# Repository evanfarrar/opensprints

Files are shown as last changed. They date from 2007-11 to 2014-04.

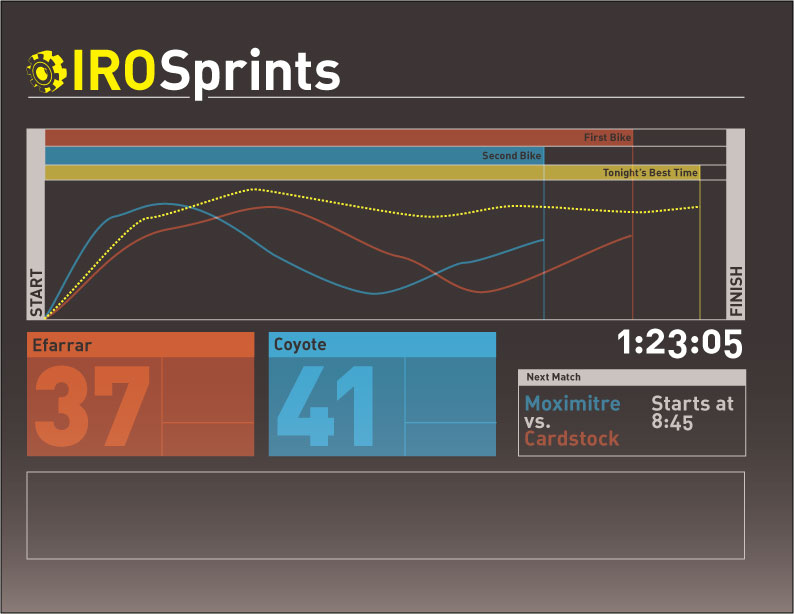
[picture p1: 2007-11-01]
doc/interface_mockups/mockup.png

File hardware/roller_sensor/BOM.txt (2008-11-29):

Qty	Descr					Mfr			Mfr P/N			Vendor		Vendor P/N	
---	-------------------		-------		-----------		-------		------------
1	hall effect switch		Allegro		A3245LUA-T		digikey		620-1213-ND
1	RJ45 modular jack		tyco		5555164-1		digikey		5555164-1
														mouser		571-5555164-1
1	5mm Red or Blue LED									digikey		365-1180-ND
1	330 ohm resistor
	(for Red LED)
	or
	100 ohm resistor									digikey		100EBK-ND
	(for Blue LED)
1	1 uF bypass cap										digikey		478-3192-ND or 490-3810-ND
2

http://search.digikey.com/scripts/DkSearch/dksus.dll?Detail?name=620-1213-ND
http://search.digikey.com/scripts/DkSearch/dksus.dll?Detail?name=A31442-ND
http://search.digikey.com/scripts/DkSearch/dksus.dll?Detail?name=365-1180-ND
http://search.digikey.com/scripts/DkSearch/dksus.dll?Detail?name=100EBK-ND
http://search.digikey.com/scripts/DkSearch/dksus.dll?Detail?name=478-3192-ND

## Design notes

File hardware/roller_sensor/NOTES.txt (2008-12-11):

NOTES:
 * board dimensions: 1.4" x 2"

TODO: for v2:
 * schematic:
   - 
 * board:
   - silk screen labels 
 * source repository: 
   - get rid of .cam file not being used.
   - create Makefile
     -- make schem-print
     -- make schem-pdf
     -- make board-print
     -- make board-pdf
     -- make gerb (moves created files to gerber/ dir) 
     -- make archive

DONE:
 * now has 2 LEDs
   - one 5 mm LED for signaling when the HE sensor is triggered.
   - one 3 mm LED for power indicator.
   - make grid of through-hole pads. qty = 7 * 14 - 12
 * board:
   - resistors should lie down instead of standing up, per the request of Jonathan Morrison.
   - new board dimensions 1.4" x 2.0"
   - make grid of through-hole pads. qty = 7 * 14 - 12
 * only 1 screw hole

misc notes:
 * Ethernet cable wiring:
   - http://en.wikipedia.org/wiki/10BASE-T
   - http://en.wikipedia.org/wiki/8P8C#Applications

Barebonespcb.com
#  2-layer, FR-4, 0.062" thick
# All-holes-plated
# 6-mil line/gap minimum
# Tin finish over 1-oz Copper
# No internal routing or scoring
(including mouse bites)
# Cut to rectangle shape only
# No mask
# No legend
# Min size 1.25" X 1.25"
# Max size 12" X 16" or 192 sq. in.
# Gerber 274X preferred
# Excellon drill (English Units)
# Minimum hole size 0.015

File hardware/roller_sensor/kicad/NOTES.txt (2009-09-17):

printing:
To print a drawing of the layout, print to pdf with X and Y scaling 1.0. Then print the generated PDF at 1.077 scale.

The mounting hole is a single pad with diameter 0.26" with a pad diameter 0.26".

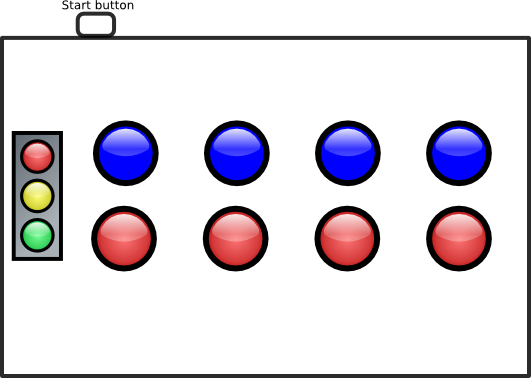
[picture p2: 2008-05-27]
doc/interface_mockups/physical_mock2.png

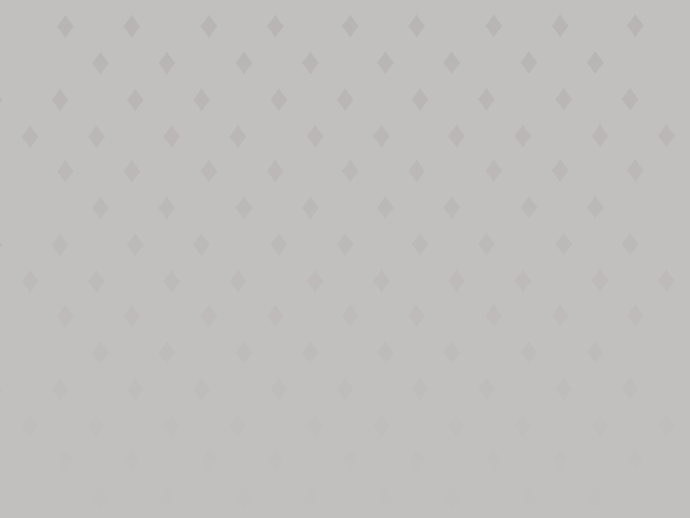
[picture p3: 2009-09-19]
media/skins/math_rash/background_menus.png

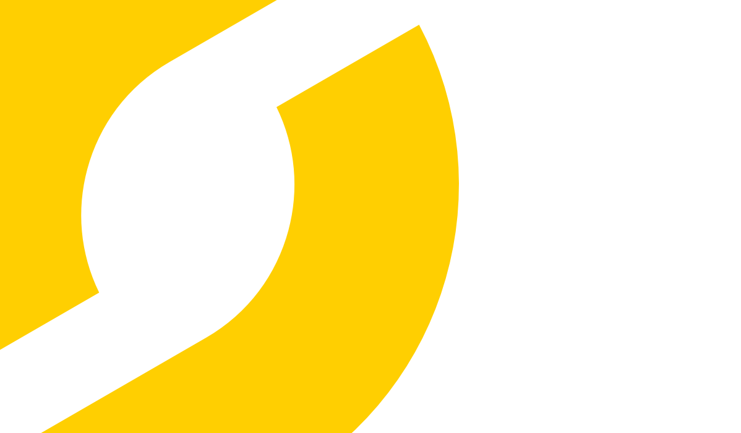
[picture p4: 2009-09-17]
media/background.png

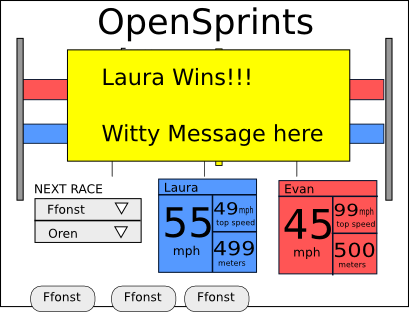
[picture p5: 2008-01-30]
doc/interface_mockups/2.0/after_race.png

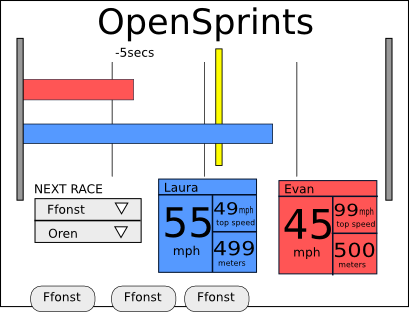
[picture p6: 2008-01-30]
doc/interface_mockups/2.0/in_progress.png

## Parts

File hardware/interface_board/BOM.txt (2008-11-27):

Qty   Descr                   Mfr         Mfr P/N         Supplier    Supplier P/N	
---   ------------------      -------     -------------   ---------   ------------
1     plastic box             Serpac      A31             Digi-Key    SRA31G-ND
4     RJ45 modular jack       tyco        5555164-1       Digi-Key    5555164-1
                                                          Mouser      571-5555164-1

2     male breakaway
      headers 8 pos

2     male breakaway
      headers 6 pos

x     hook-up wire

(Optional:)

2     screw terminal
      blocks

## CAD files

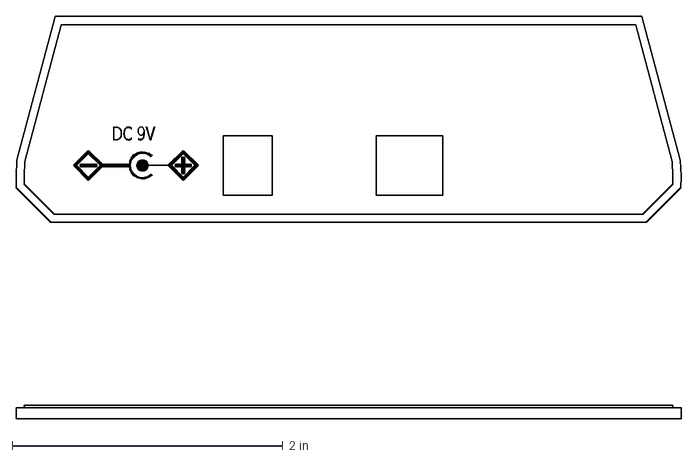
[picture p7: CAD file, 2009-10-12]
hardware/a-31_modifications/panel-arduino_text.dxf
DC\~9V

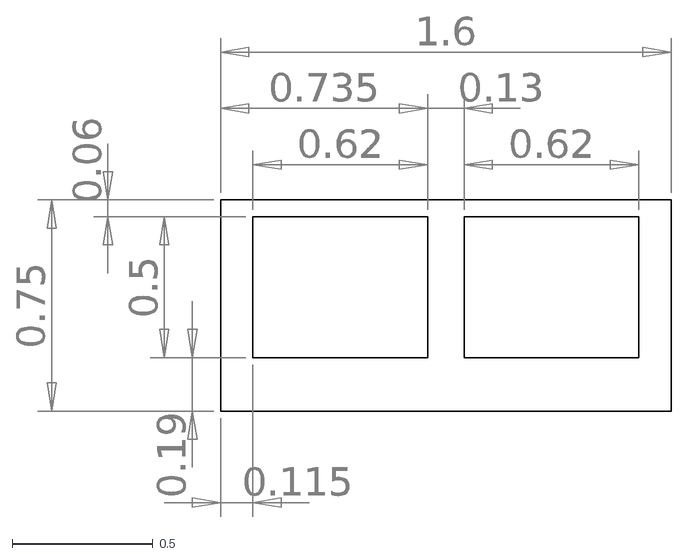
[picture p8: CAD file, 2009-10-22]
hardware/c-6_modifications/c-6_RJ45_cutouts.dxf
0.75
0.06
0.5
0.19
1.6
0.735
0.13
0.62
0.115

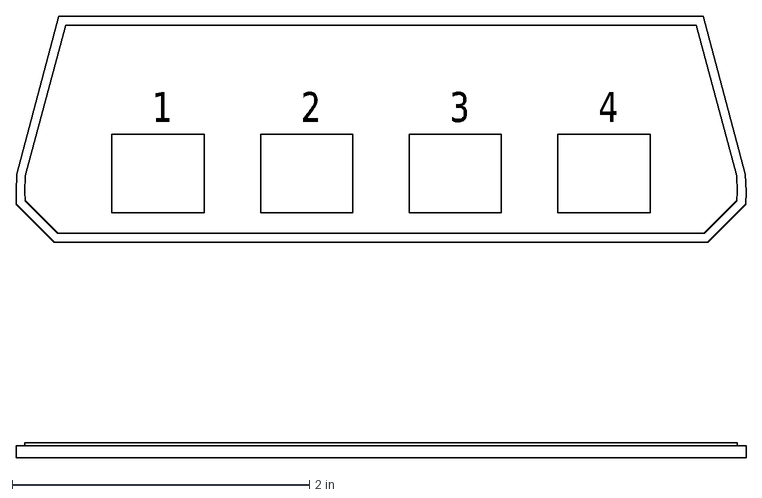
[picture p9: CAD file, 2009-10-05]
hardware/a-31_modifications/panel-sensors_text.dxf
1
2
3
4

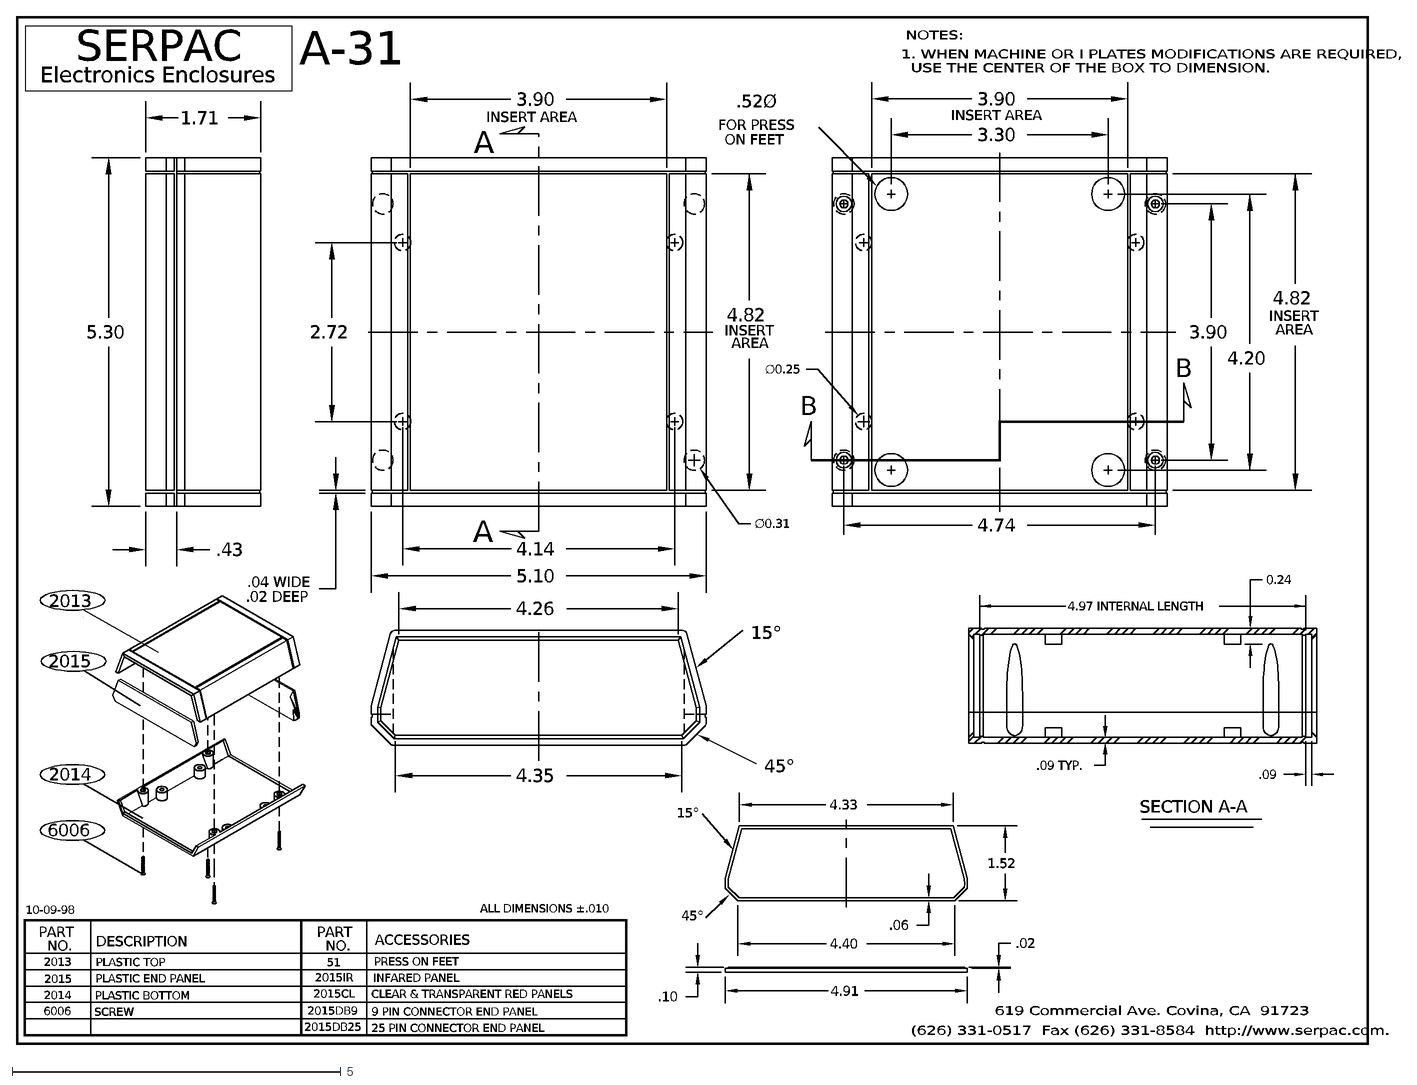
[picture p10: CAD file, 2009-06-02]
hardware/a-31_modifications/a-31.dxf
1.52
(626) 331-0517 Fax (626) 331-8584 http://www.serpac.com.
PLASTIC BOTTOM
PLASTIC TOP
DESCRIPTION
PLASTIC END PANEL
2014
6006
2013
2015
NO.
SCREW
10-09-98
PART
ALL DIMENSIONS ±.010
CLEAR & TRANSPARENT RED PANELS
2015CL
2015IR
51
ACCESSORIES
PRESS ON FEET
INFARED PANEL
4.35
45°
.10
15°
4.91
4.40
4.33
.06
619 Commercial Ave. Covina, CA 91723
SECTION A-A
.02
.09 TYP.
.09
3.90
3.30
INSERT AREA
USE THE CENTER OF THE BOX TO DIMENSION.
4.74
1. WHEN MACHINE OR I PLATES MODIFICATIONS ARE REQUIRED,
SERPAC
Electronics Enclosures
5.30
2.72
.43
.02 DEEP
.04 WIDE
4.26
A
5.10
4.14
A-31
1.71
INSERT
4.82
AREA
B
ON FEET
FOR PRESS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

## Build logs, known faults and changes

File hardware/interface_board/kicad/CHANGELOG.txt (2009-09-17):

---------------------------------------------------
v2.3.2 2009.09.13
---------------------------------------------------
gerbers generated with Pcbnew Build: SVN-R1805 (20090603)

Changes:

    * added blink LED to design
	* designed for soldermask and silkscreen for the first time.
	* font has curves

---------------------------------------------------
v2.2
---------------------------------------------------

Changes:

    * FIXED: The Arduino's power jack doesn't poke through the end panel of the enclosure.
          o Moves the Arduino out 0.05". 
    * improved indication of the columns of holes where the male headers are installed.
    * now text says "opensprints.org" instead of "OpenSprints". 

---------------------------------------------------
Previous version: v2.1
---------------------------------------------------

Changes:

    * Arduino placement moved so it fits better inside the enclosure.
    * Mounting holes for affixing the Arduino to the board with small nuts and bolts.
    * "top" and "bottom" labels.
    * Aesthetic changes to the title text. 

Bugs:

    * The Arduino's power jack doesn't poke through the end panel of the enclosure. 

---------------------------------------------------
Previous version: v2
---------------------------------------------------
Changes:

    * Phased out UBW support.
    * Designed to fit a specific plastic project box.
    * Moved the placement of the RJ45 jacks to provide better access to the tabs. 

Bugs:

    * The Arduino is positioned too far out. A slot must be routed out of the end panel to fit the panel in the enclosure. 

---------------------------------------------------
First version: v1
---------------------------------------------------

This version supported both the UBW and the Arduino microcontroller boards. NOTE: V1 interface board rework

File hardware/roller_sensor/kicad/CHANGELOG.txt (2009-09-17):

v2.2.3 2009.09.13
---------------------------------------------------
gerbers generated with Pcbnew Build: SVN-R1805 (20090603)

Changes:

    * VOUT and VCC signals going to hall effect sensors can now be swapped in order to allow the user to install hall effect sensor backwards, which swaps the magnetic pole that the sensor senses.
	* designed for soldermask and silkscreen for the first time.
	* font has curves

v2.1
---------------------------------------------------
Changes:

    * Sensor indicator LED wiring issue was corrected.
    * "top" and "bottom" labels. 

Bugs:

    * TBD 

v2
---------------------------------------------------
Changes:

    * Designed to fit a specific plastic project enclosure.
    * Added power indicator LED.
    * Moved the placement of the RJ45 jacks to provide better access to the tabs. 

Bugs:

    * Ouch! The sensor trigger indicator LED was wired incorrectly. 

First version: v1
---------------------------------------------------
Worked fine, wired correctly.

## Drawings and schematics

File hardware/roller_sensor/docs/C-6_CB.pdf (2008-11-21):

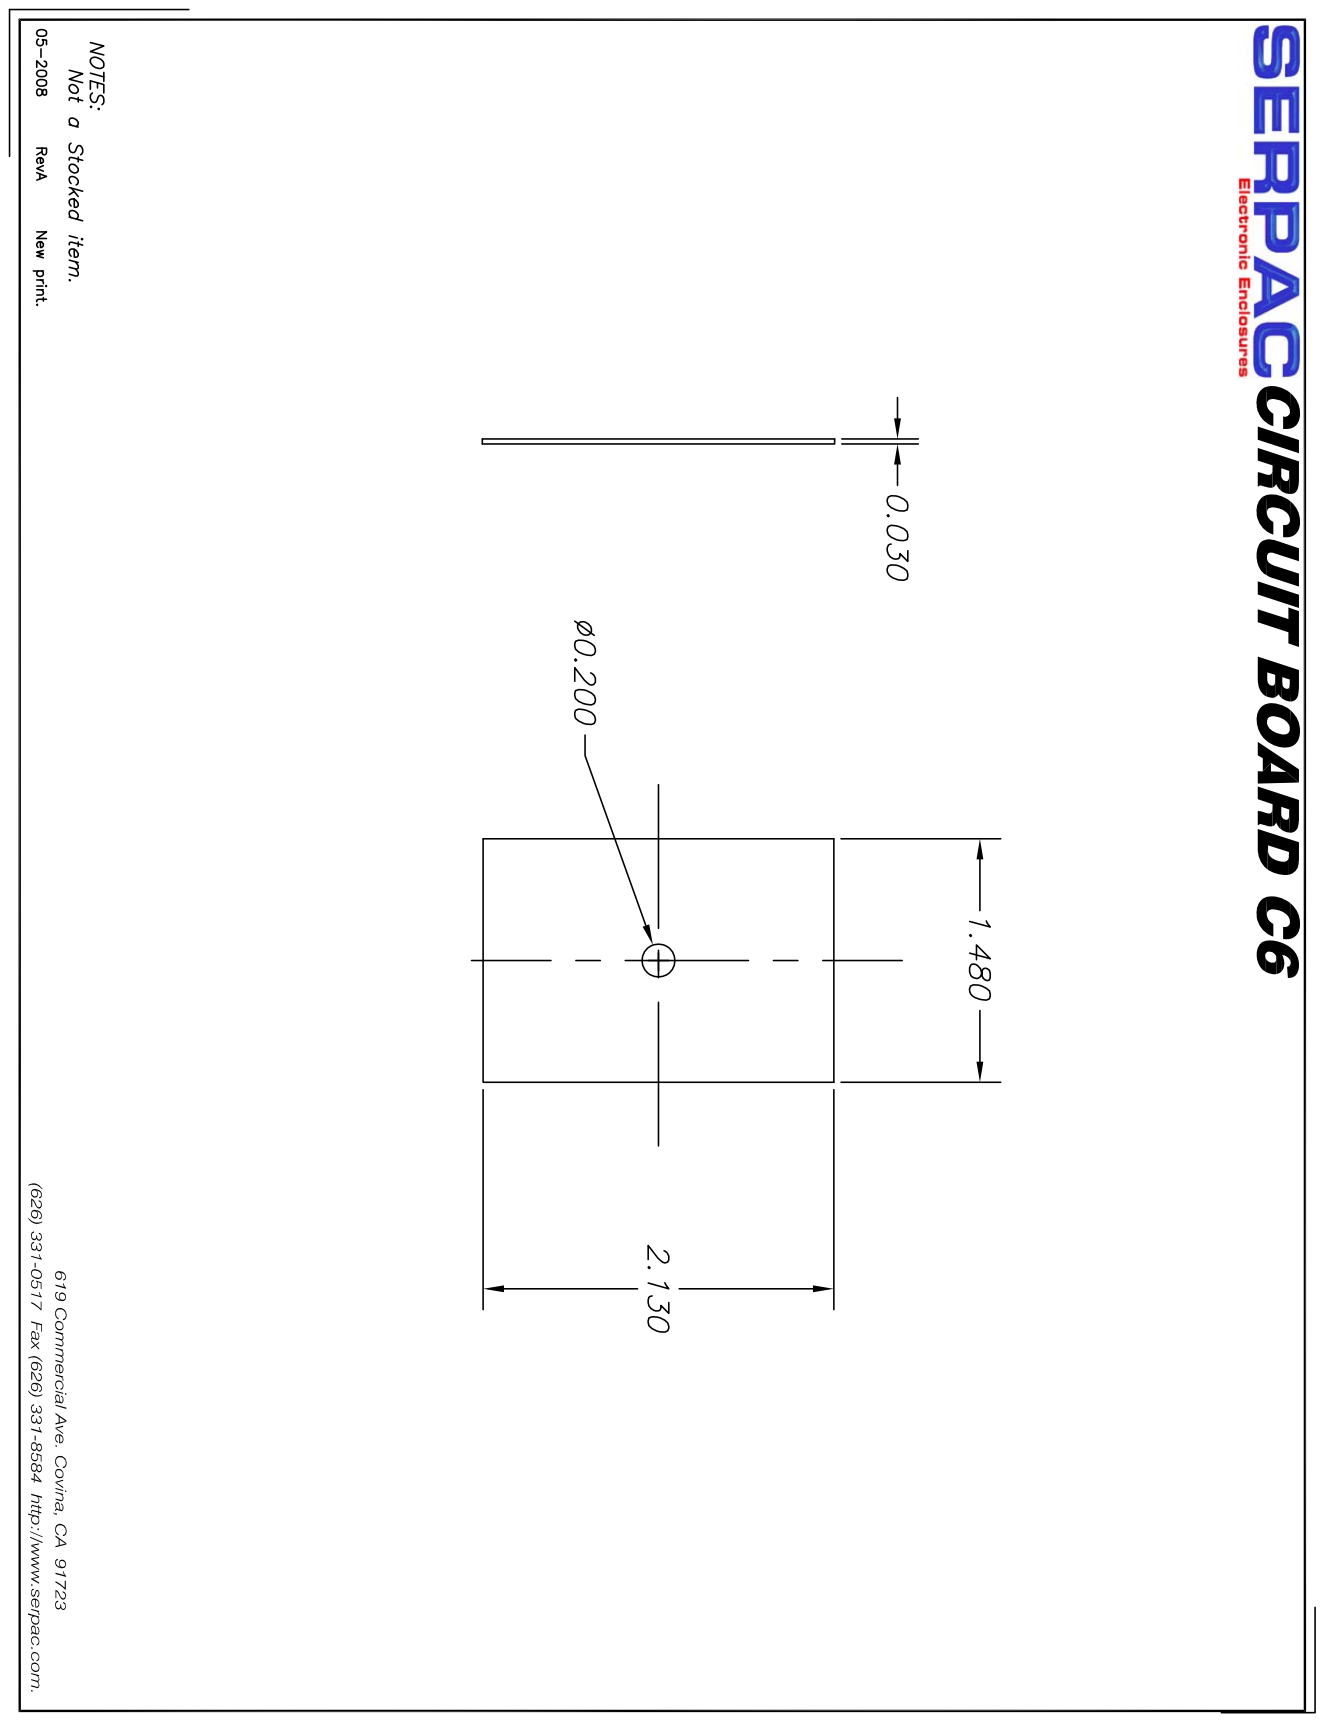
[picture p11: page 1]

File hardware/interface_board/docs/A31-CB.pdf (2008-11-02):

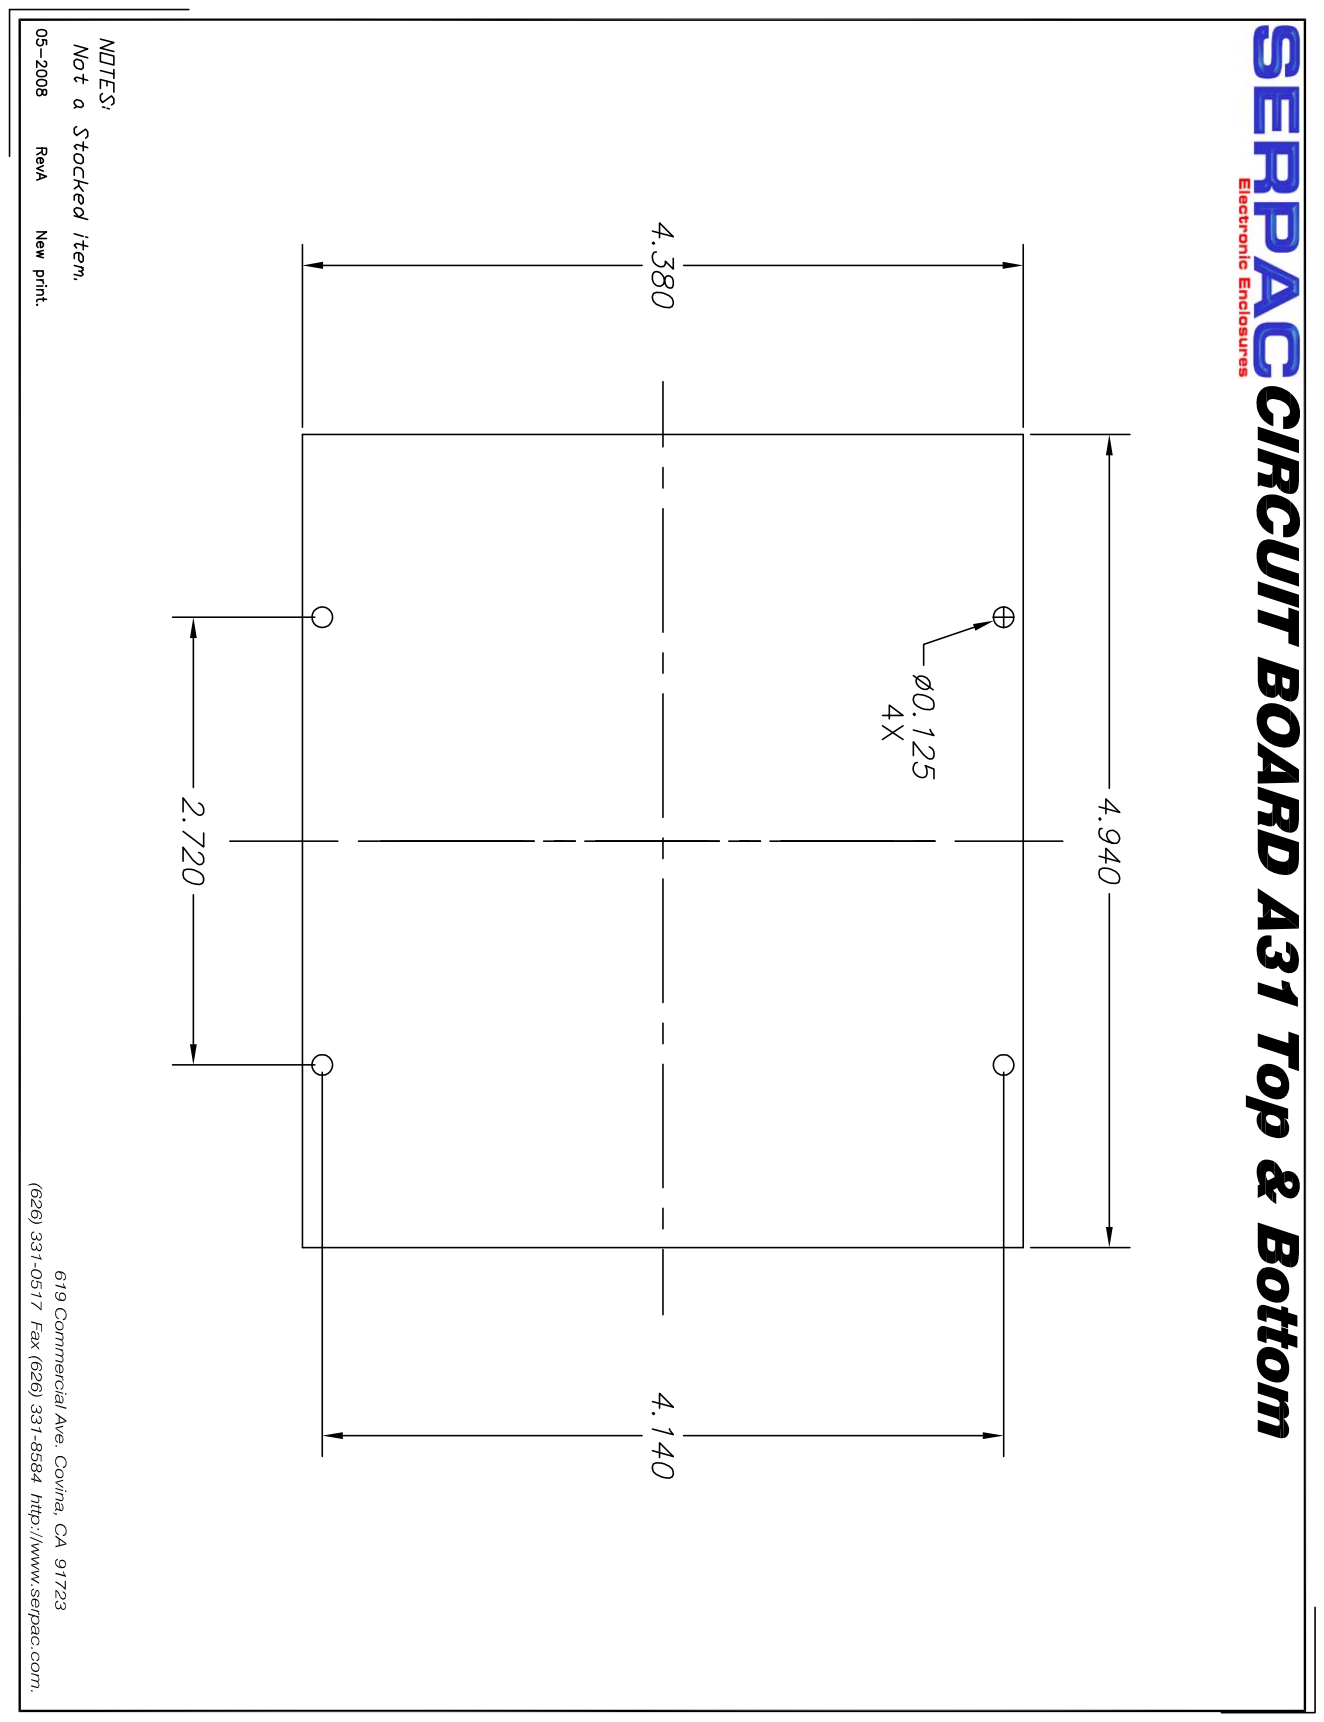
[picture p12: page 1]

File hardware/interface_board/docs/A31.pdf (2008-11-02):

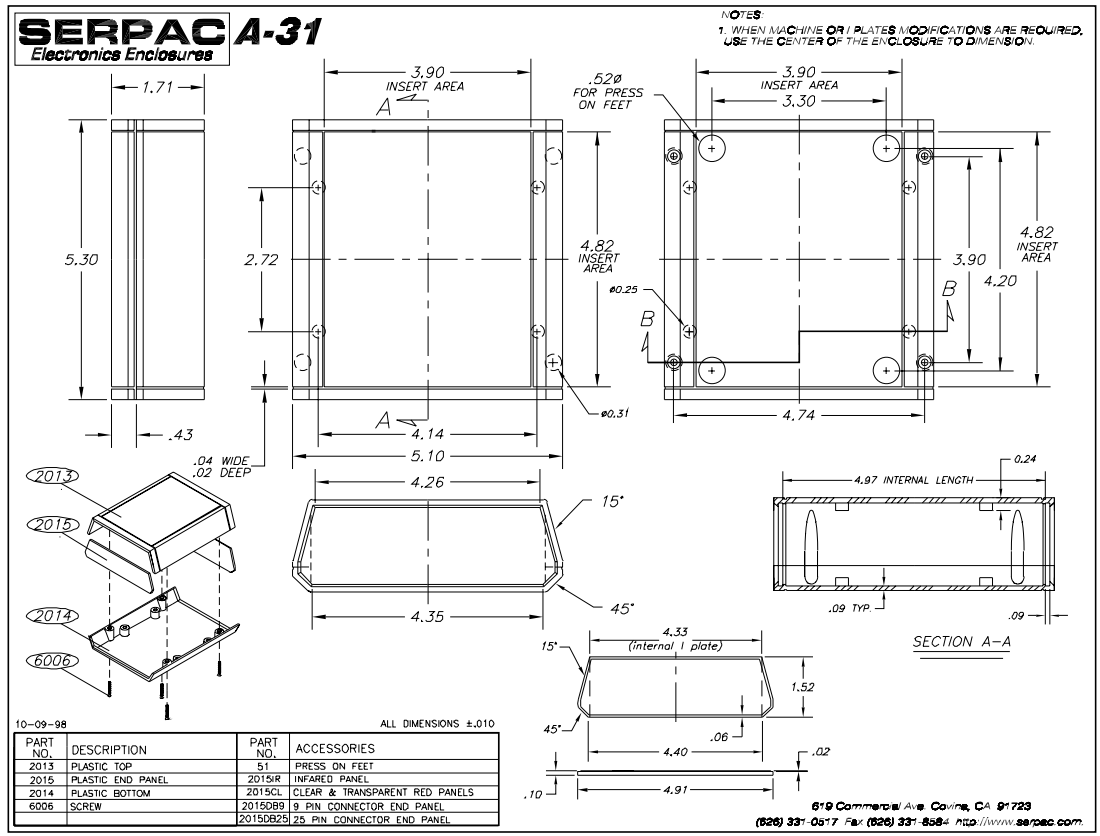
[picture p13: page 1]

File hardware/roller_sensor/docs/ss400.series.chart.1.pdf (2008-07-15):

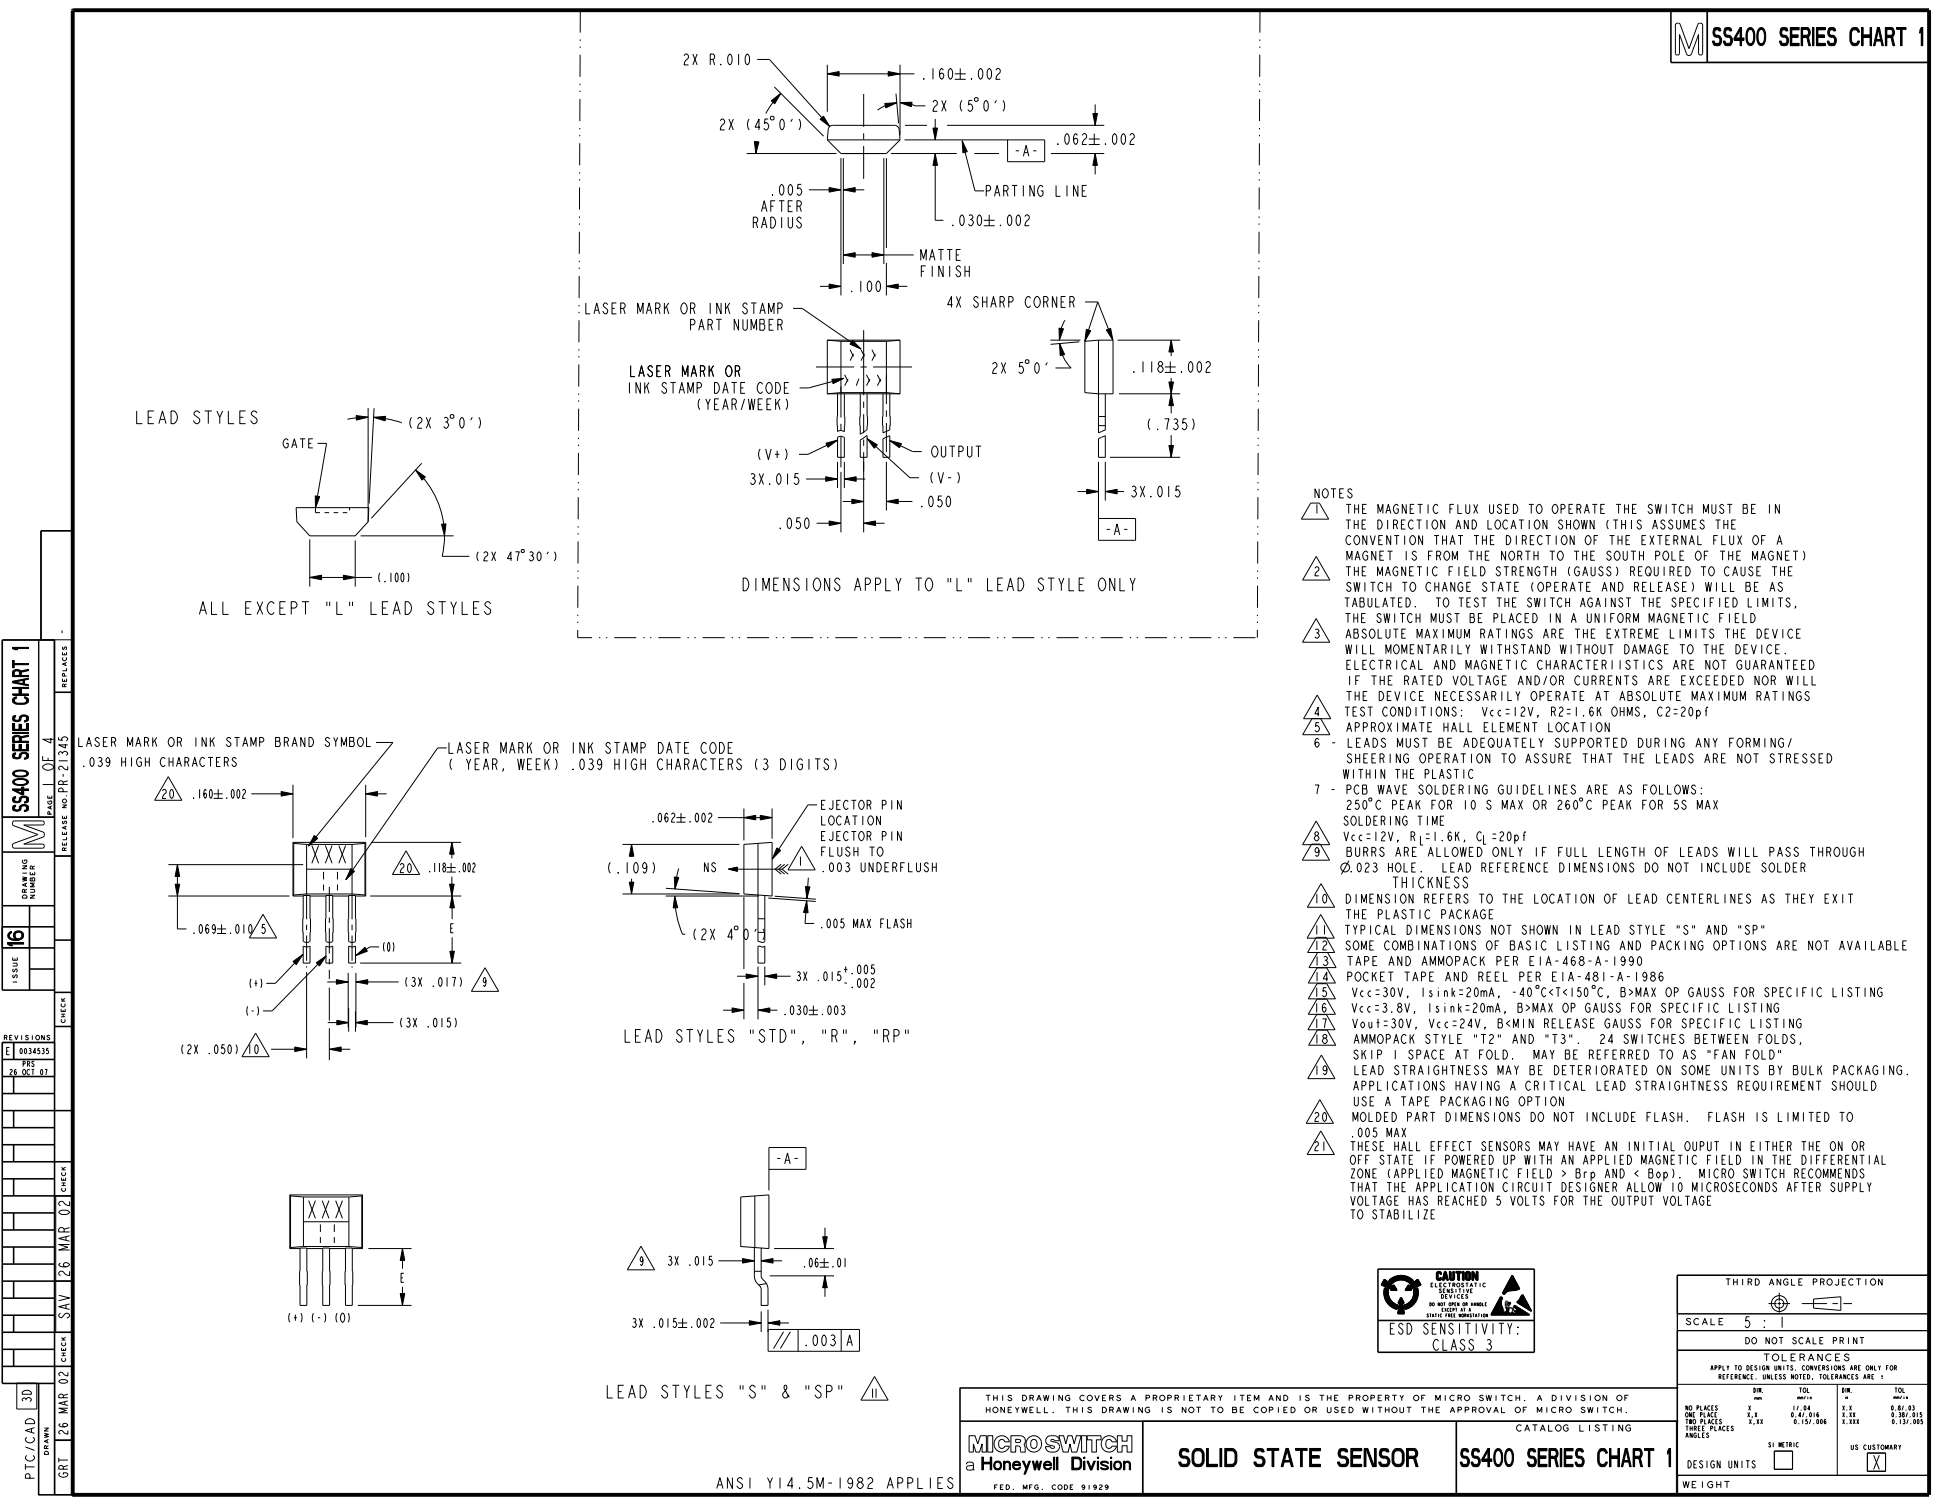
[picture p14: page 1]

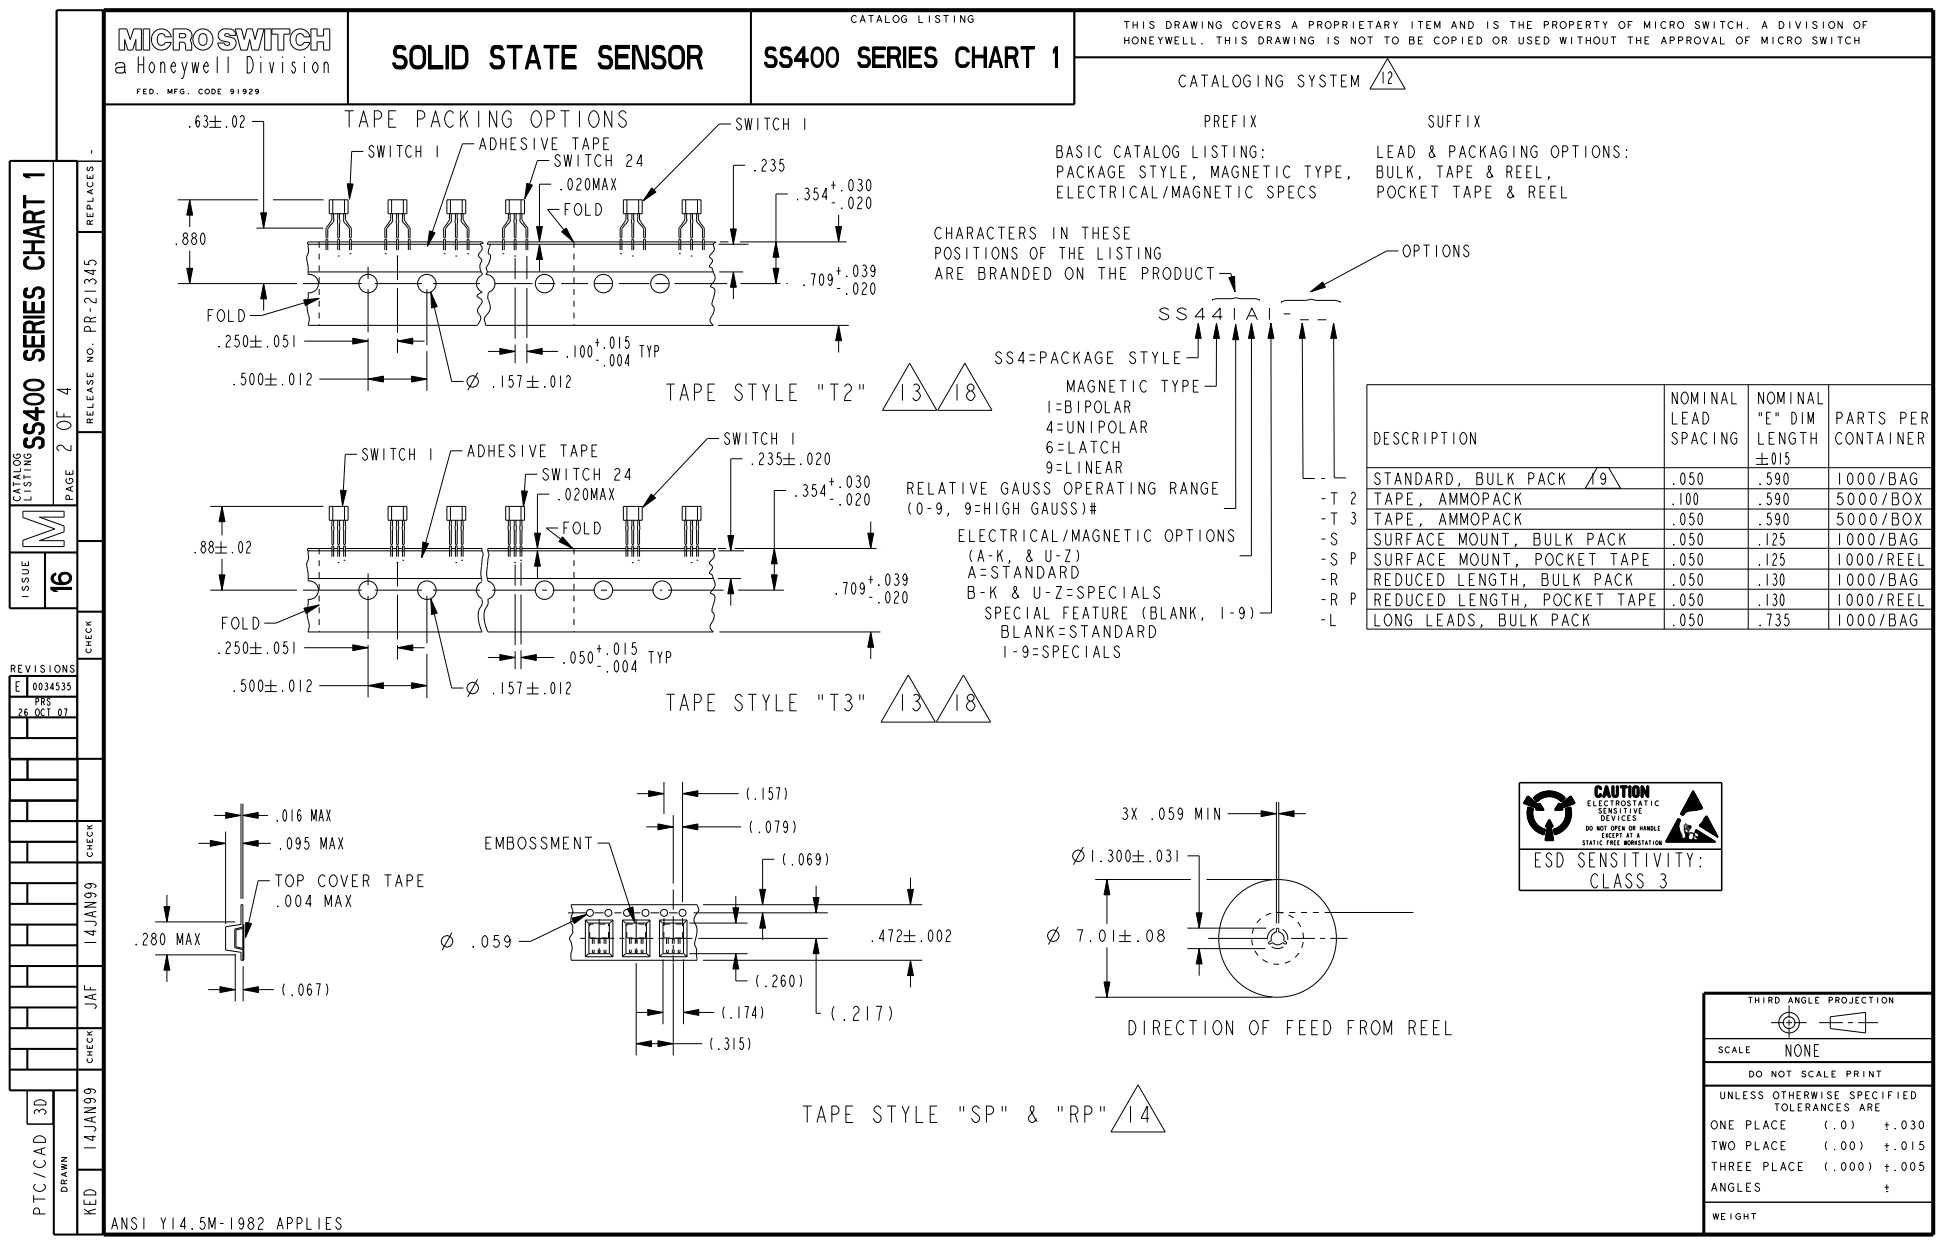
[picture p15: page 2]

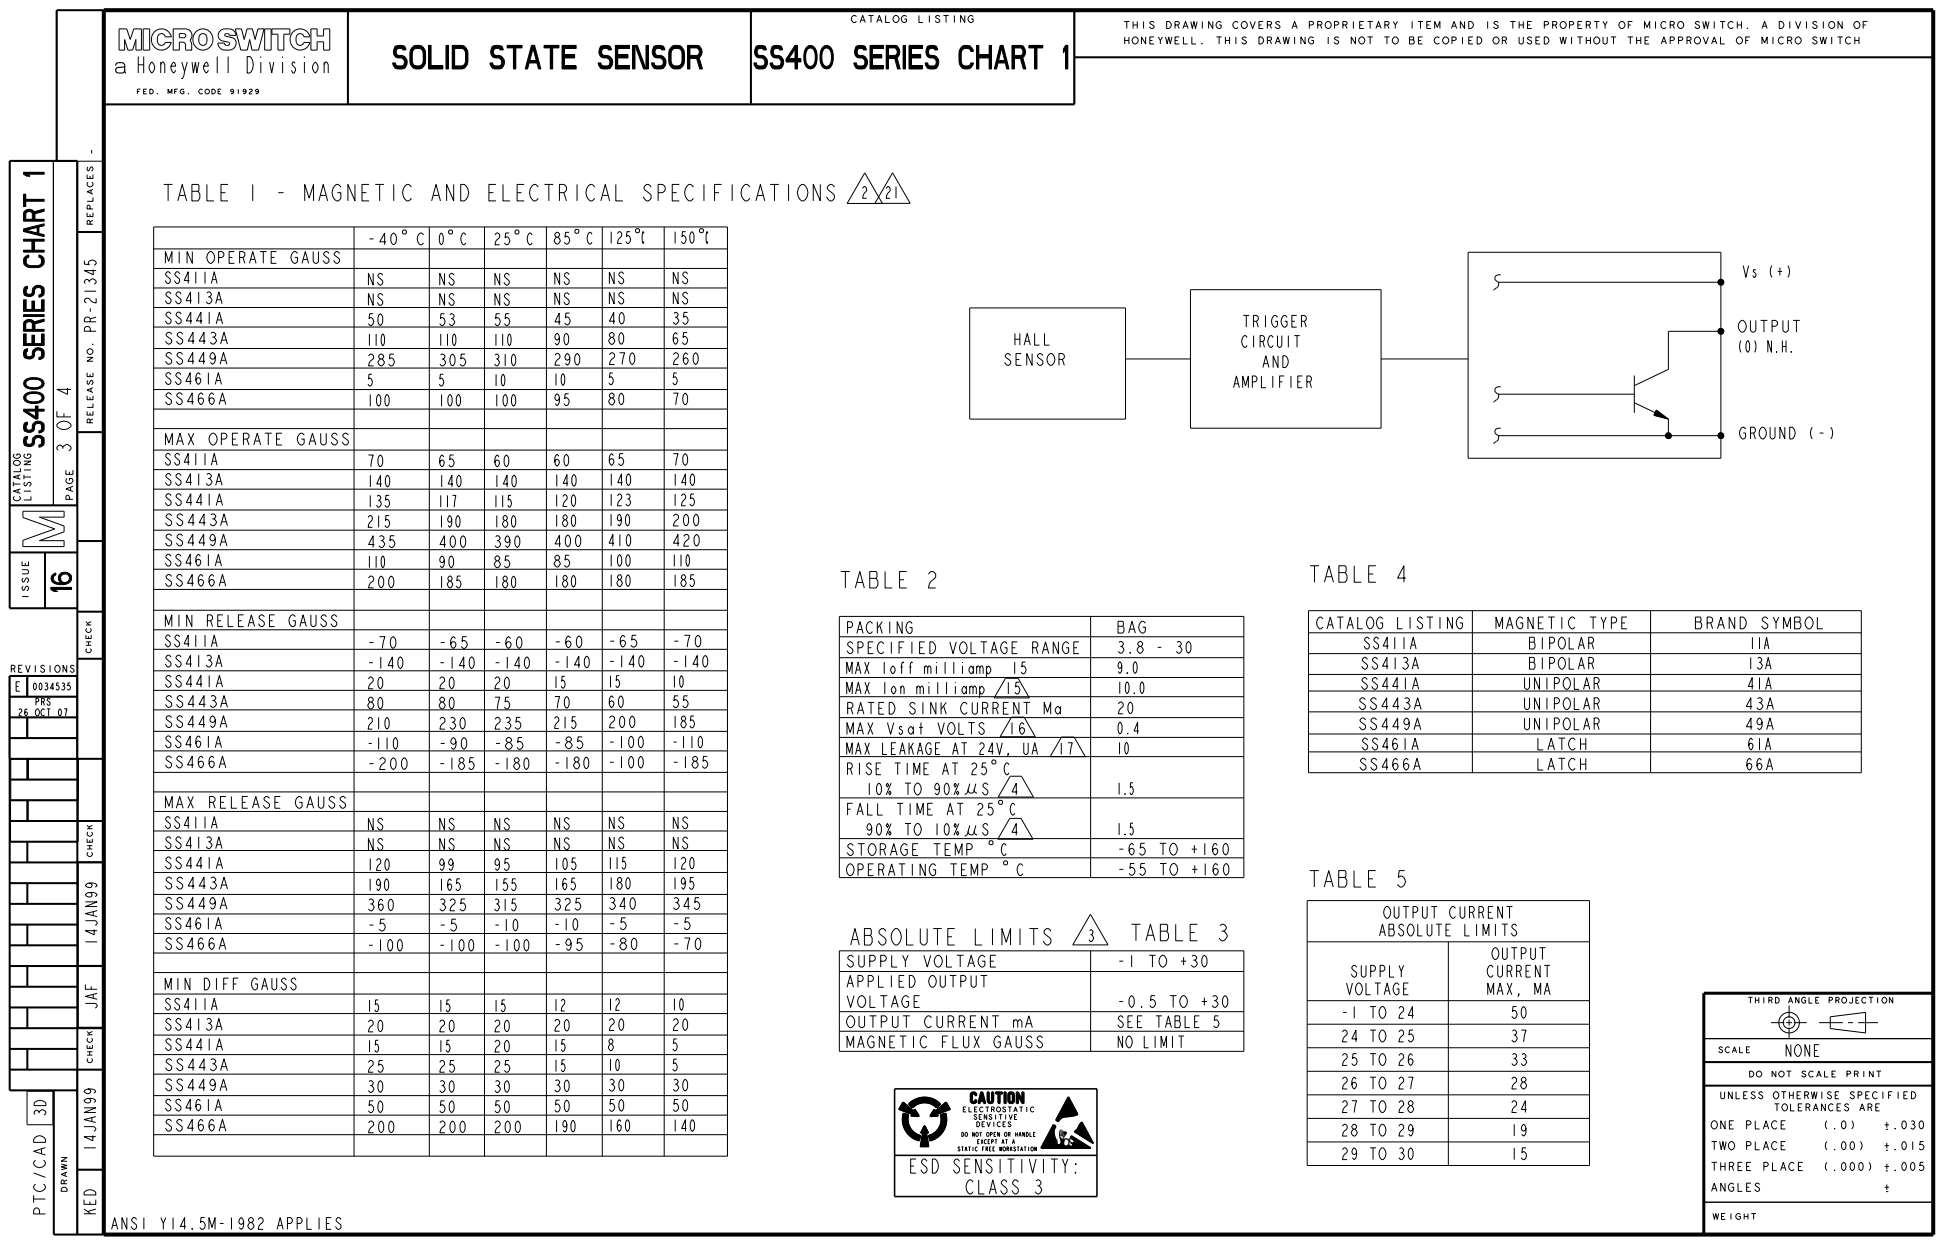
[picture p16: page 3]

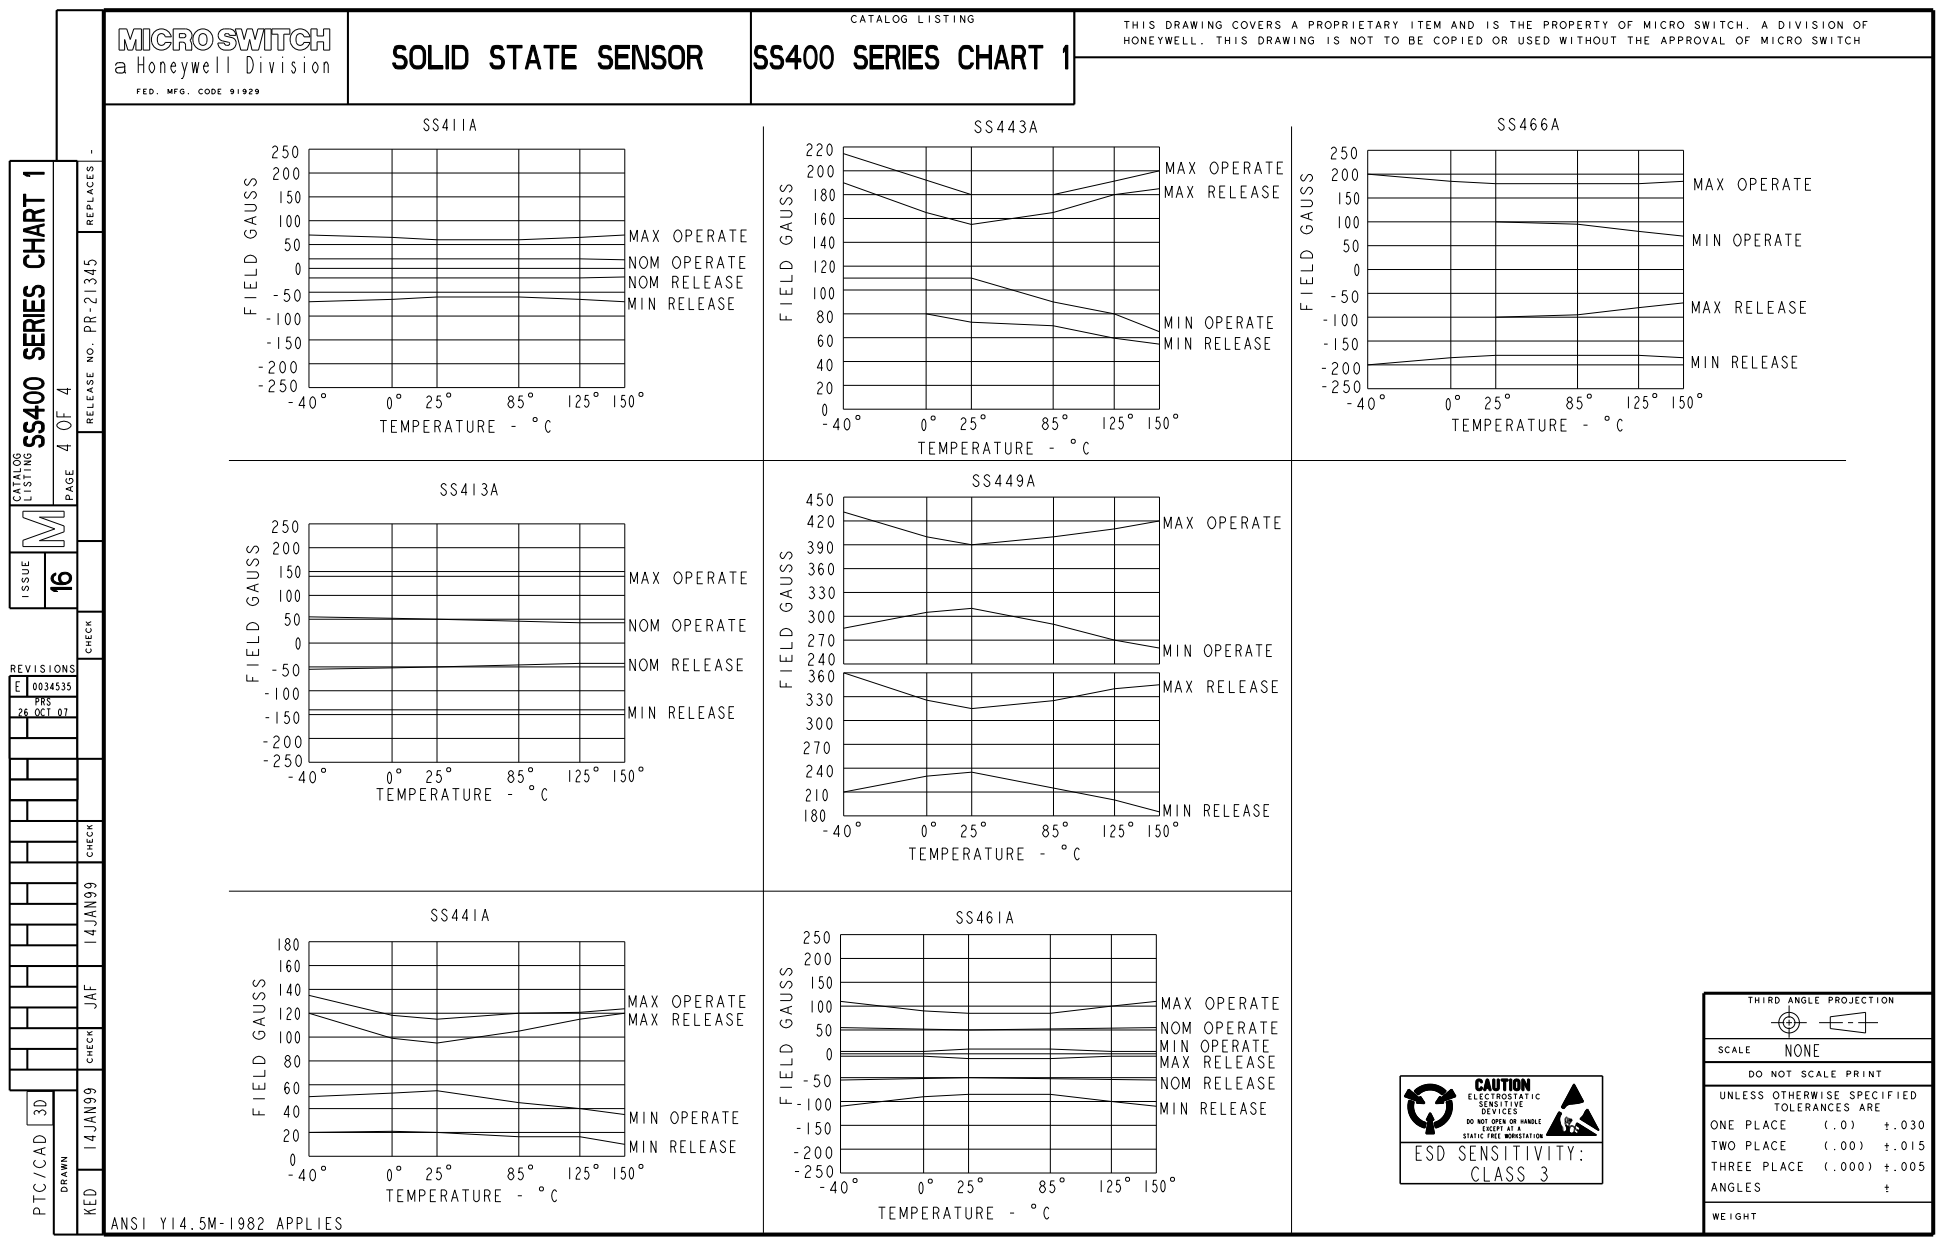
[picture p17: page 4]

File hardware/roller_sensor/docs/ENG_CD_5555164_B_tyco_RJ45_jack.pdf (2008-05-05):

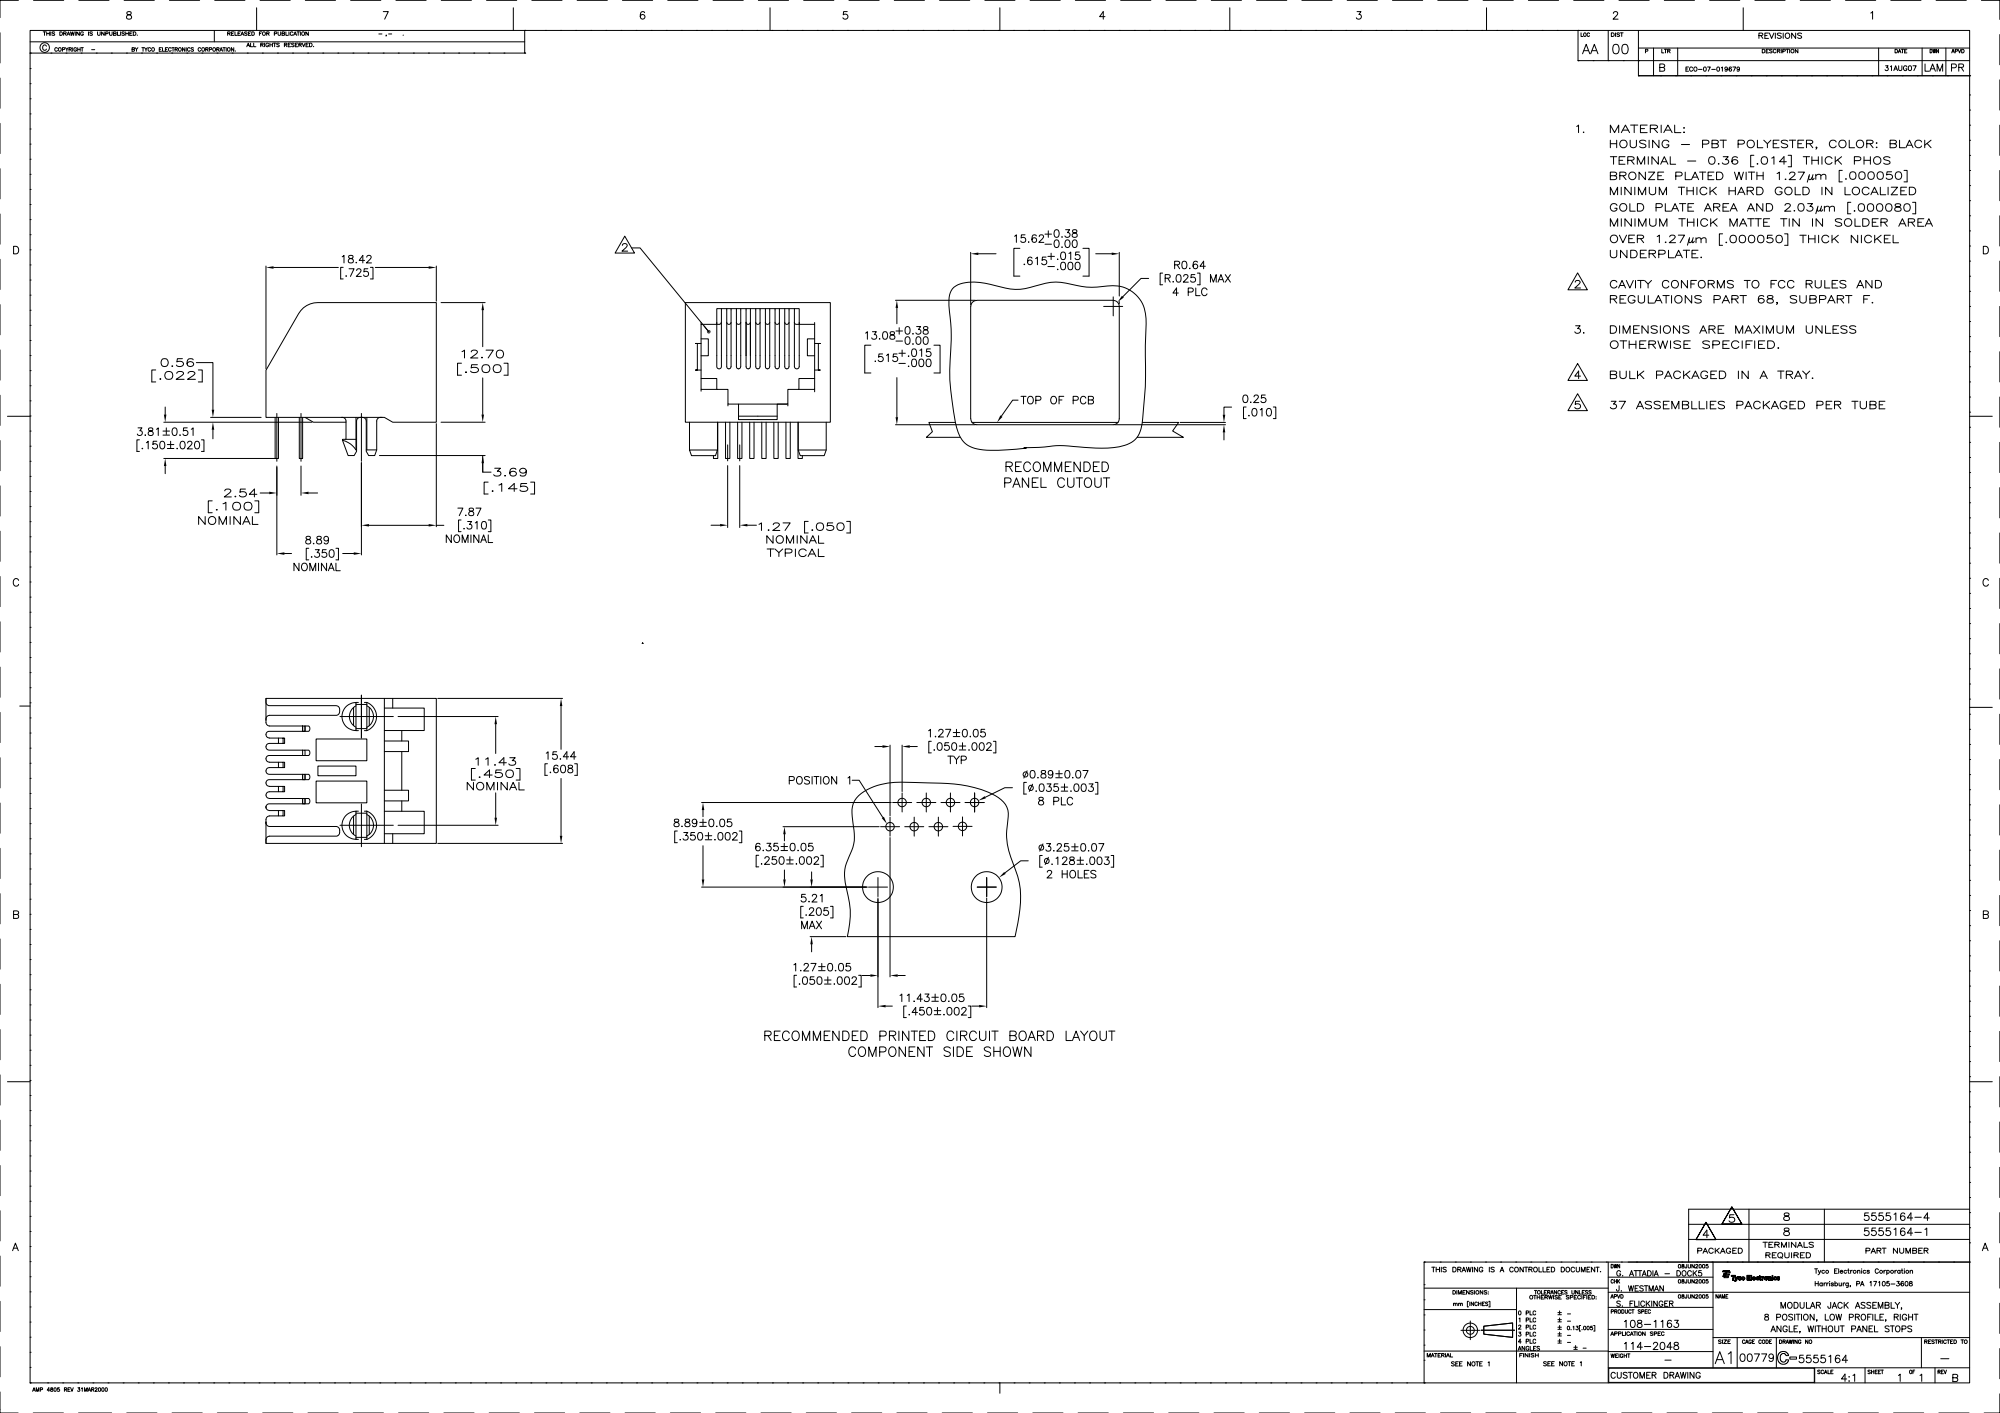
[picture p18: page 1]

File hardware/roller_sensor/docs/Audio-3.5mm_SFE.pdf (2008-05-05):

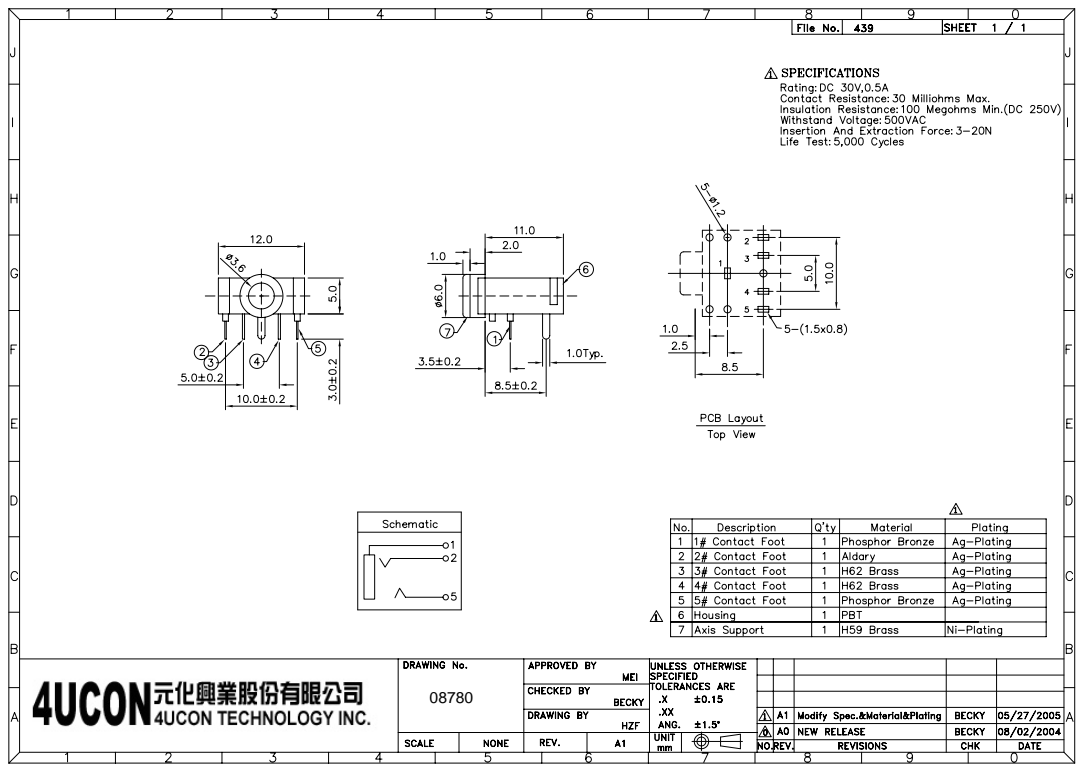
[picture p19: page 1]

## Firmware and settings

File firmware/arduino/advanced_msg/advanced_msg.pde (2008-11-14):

#undef int
#include <stdio.h>

#define TOGGLE_IO 9 //Arduino pin to toggle in timer ISR, used for debug
#define BUTTON_PIN 6
#define SENSOR_0_PIN 2   //
#define SENSOR_1_PIN 3   //
#define SENSOR_2_PIN 4   //
#define SENSOR_3_PIN 5   //
#define TICK_PACKET_MAX_SIZE 1
#define RACE_PACKET_SIZE 55  // buffer allocation for the race packet
#define RACE_PACKET_UTIL_SIZE 54 // buffer utilization for the race packet (keep this as low as possible to reduce overrun risk)

int statusLEDPin = 13;
long statusBlinkInterval = 250;
int lastStatusLEDValue = LOW;
long lastStatusBlinkMillis = 0;

boolean val0 = true;
boolean val1 = true;
boolean val2 = true;
boolean val3 = true;
boolean buttonPinVal = true;
boolean inputChange = false;

char sensorBuff = 0;

char strDebug[2];
char* p_Debug = strDebug;
char strRacePacket[RACE_PACKET_SIZE];
char* p_RacePacket = strRacePacket;
char strTXRacePacket[RACE_PACKET_SIZE];  // the TX buffer so we can reuse the RacePacket as soon as it fills
char* p_TXRacePacket = strTXRacePacket;

boolean sendRacePacketNow = true;  // Start by sending a blank packet
boolean buttonNow = false;

int lastWinnerLEDValue = LOW;
long lastWinnerBlinkMillis = 0;

boolean raceStarted = false;
boolean raceStarting = false;
boolean mockMode = false;
unsigned long raceStartMillis;
unsigned long currentTimeMillis;
////////////////////////////////////////////////////////


boolean lastSensor0Value = true;
boolean lastSensor1Value = true;
boolean lastSensor2Value = true;
boolean lastSensor3Value = true;
boolean lastButtonValue = true;

boolean racer1TickNow = false;
boolean racer2TickNow = false;
boolean racer3TickNow = false;
boolean racer4TickNow = false;


unsigned long racer1Ticks = 0;
unsigned long racer2Ticks = 0;
unsigned long racer3Ticks = 0;
unsigned long racer4Ticks = 0;

void handleInputChange(){

  inputChange = false;
}



/////////////////////////////////////////////////////////////////////////////////////////////
// MORGAN's new version using CTC -- magic numbers from the datasheet, sorry.
//
//Setup the PCICR  --  PCIE2 for port D
//Configures pin-change interrupt on port D

void SetupPinChangeInterrupts(){

  PCICR = 0b00000100;  // pin change interrupt on port D only (the sensor pins);
  PCMSK2 = 0b00111100; // enable pin interrupts PCINT18..21 (arduino I/O pins 2 3 4 5)

}


void blinkLED() {
  long num = millis();
  if (num - lastStatusBlinkMillis > statusBlinkInterval) {
    lastStatusBlinkMillis = num;

    if (lastStatusLEDValue == LOW)
      lastStatusLEDValue = HIGH;
    else
      lastStatusLEDValue = LOW;

    digitalWrite(statusLEDPin, lastStatusLEDValue);
  }

}

//////////////////////////////////////////////////////////////////////////////////
// checkSerial()
// Handles all command inputs from the PC for lighting, race start, timing, etc
// 'g' :  GO.  Resets racerTicks and should probably reset the clock or at least the Race Time.
// 'm' :  MOCK.  Starts a mock sensor data mode -- need to re-code this to output a reasonable sensor frequency
// 's'  :  STOP MOCK.  Stops the race, and turns off Mock Mode if it's on.
// 'L'  :  LIGHT.  Should be implemented to parse arbitrary light commands (format TBD)
//////////////////////////////////////////////////////////////////////////////////
void checkSerial(){
  char val;
  if(Serial.available()) {
    val = Serial.read();
    if(val == 'g') {
      Serial.println("gACK\n");
      cli();
      raceStartMillis = millis();
      sei();
      racer1Ticks = 0;
      racer2Ticks = 0;
    }
    if(val == 'm') {
      mockMode = true;
    }
    if(val == 's') {

      mockMode = false;
    }
  }
}

/////////////////////////////////////////////////////////////////////////////////////////////////
// the old, busted checkButton routine was a naughty poller -- should use a GPIO Interrupt instead
// this new, hotness one acts on a flag set in the interrupt-on-change for the button.
/////////////////////////////////////////////////////////////////////////////////////////////////
void checkButton(){
  if (buttonNow){
      racer1Ticks = 0;
      racer2Ticks = 0;
  }
  buttonNow = false;
}


void clearTXRacePacket(){
  int i;
  for (i=0; i < RACE_PACKET_SIZE; i++)
  {
    strTXRacePacket[i] = 0;
  }
}


void clearRacePacket(){
  int i;
  for (i=0; i < RACE_PACKET_SIZE; i++)
  {
    strRacePacket[i] = 0;
  }
}

/////////////////////////////////////////////////////////////////////////////////////////////
// MORGAN's new version using CTC -- magic numbers from the datasheet, sorry.
//
//Setup Timer2.
//Configures the ATMega168 8-Bit Timer2 to generate an interrupt
//at a frequency of 1 millisecond exactly (to about 1% accuracy)
//No return value.
//See the example usage below.

void SetupTimer2For2Milli(){

  //Timer2 Settings: Timer Prescaler /128, mode 2 = CTC
  //Timer clock = 16MHz/128 = 125kHz or 8us ticks
  //The /128 prescale gives this increment
  //so we just hard code this for now.

  TCCR2A = 0b00000010;  // no output compare, just CTC mode set by WGM22,21,20;
  TCCR2B = 0b00000101;  // prescaler = 128
  OCR2A = 0xFA;  //7D = 125 counts for 1millisecond with /128 prescaler -- 2ms at FA
  TIMSK2 = 0b00000010;  // enable OCR2A compare interrupt (this is our 2ms interrupt), disable OCR2B and overflow
  TCNT2=0;
}

void SetupPinChangeLogic(){
  val0 = digitalRead(SENSOR_0_PIN);
    val1 = digitalRead(SENSOR_1_PIN);
    val2 = digitalRead(SENSOR_2_PIN);
    val3 = digitalRead(SENSOR_3_PIN);
    buttonPinVal = digitalRead(BUTTON_PIN);
    lastSensor0Value = val0;  // now that you've used this value of val#, make sure it's recorded as the standing value...
    lastSensor1Value = val1;
    lastSensor2Value = val2;
    lastSensor3Value = val3;
    lastButtonValue = buttonPinVal;

}

void setup() {
  cli();
  clearRacePacket();
  clearTXRacePacket();
  Serial.begin(115200);
  Serial.println("Setup starting");
  SetupTimer2For2Milli();
  SetupPinChangeInterrupts();
  pinMode(statusLEDPin, OUTPUT);
  pinMode(TOGGLE_IO, OUTPUT);
  pinMode(SENSOR_0_PIN, INPUT);
  pinMode(SENSOR_1_PIN, INPUT);
  pinMode(SENSOR_2_PIN, INPUT);
  pinMode(SENSOR_3_PIN, INPUT);
  pinMode(BUTTON_PIN, INPUT);
  digitalWrite(BUTTON_PIN, HIGH);
  SetupPinChangeLogic();
  Serial.println("Setup Complete, Starting Interrupts");
  sei();
}

// STATUS:  data is now sent raw low nibble but is suffixed with '#'



long time = 0;
char strTime[10];


void loop(void) {
  blinkLED();
  //digitalWrite(TOGGLE_IO,!digitalRead(TOGGLE_IO));
  checkSerial();
  checkButton();
 // if (digitalRead(SENSOR_0_PIN)) Serial.println("$");
  if (inputChange) handleInputChange();
  if (sendRacePacketNow == true){
     strcat(p_RacePacket, "#");
     sendRacePacketNow = false;
     clearTXRacePacket();
     strcpy(p_TXRacePacket, p_RacePacket);  // copy it to the TX buffer
     clearRacePacket(); // and zero the packet
     cli();
     time = millis() - raceStartMillis; // NOTE SPRINTF %u and %i escapes FUCK UP THE TIME -- 16 bit instead of 32 bit
     sei();
     ltoa(time, strTime, 10);
     sprintf(p_RacePacket, "!%s@", strTime);  // then put the time in milliseconds into first position plus the flag character @
//     Serial.println("this is a longer string which has more letters");  // now send the buffered copy
     Serial.println(p_TXRacePacket);  // now send the buffered copy
      //Serial.println(strTime);
  }
  //digitalWrite(TOGGLE_IO,!digitalRead(TOGGLE_IO));
}


/////////////////////////////////////////////////////////////////////////////////////////////
//Timer2 CTC (c)interrupt vector handler
/////////////////////////////////////////////////////////////////////////////////////////////
ISR(TIMER2_COMPA_vect) {
//Toggle the IO pin to the other state.  DEBUG
  digitalWrite(TOGGLE_IO,!digitalRead(TOGGLE_IO));

// Packet format is '!' + time + '@' + hexadecimal representation of tickstate for each 2 milliseconds.
//

    char m = 0;                   // build a nibble containing the tickNow info
    // NOTE on interrupt disable -- if the GPIO interrupt sets a flag between saving the tickNow
    // states in "m", it could be incorrectly cleared by the following section.
    // disable interrupts for this brief period to make sure this does not happen
    // note that we do NOT disable interrupts while performing the potentially 
    // time-consuming sprintf, strcat, and strlen calls
    // The GPIO interrupts should still generally take precedence.
    sei();  
    m |= racer1TickNow;
    m |= racer2TickNow << 1;
    m |= racer3TickNow << 2;
    m |= racer4TickNow << 3;
    racer1TickNow = false;        // reset the TickNow state so we don't duplicate ticks
    racer2TickNow = false;
    racer3TickNow = false;
    racer4TickNow = false;

    m = m + 'a';


    cli();
    
    char n = 0;
    sprintf(&n,"%c", m);        // print the nibble into HEX 0123456789ABCDEF
    strcat(p_RacePacket, &n);     // add it to the buffer -- just send it raw instead?...
    int size = strlen(p_RacePacket);
    if (size > (RACE_PACKET_SIZE - 1))
    {
                //We're out of space and lost data -- should never get here
      Serial.println("Buffer Overrun during GPIO Scan");
    }
    else if (size >= (RACE_PACKET_UTIL_SIZE - TICK_PACKET_MAX_SIZE))
    {
      // Packet is full, so just in case we end up with one more in there,
      // set the flag now to transmit the packet back in the main loop
      sendRacePacketNow = true;
    }
}







/////////////////////////////////////////////////////////////////////////////////////////////
//GPIO on-change interrupt vector handler
/////////////////////////////////////////////////////////////////////////////////////////////
ISR(PCINT2_vect) {
  // We need to disable interrupts here to ensure that subsequent ticks are processed after this round
  // Cannot allow a change in state to screw up the process of checking versus previous states.
    cli();
    
    // Read each of the pins
    // This should really be done in a faster way by reading the port once to minimize ISR execution time
    // but for whatever reason, the last attempt at doing that didn't work.
    // So we'll just use the likely non-optimizing calls from the Arduino library
    val0 = digitalRead(SENSOR_0_PIN);
    val1 = digitalRead(SENSOR_1_PIN);
    val2 = digitalRead(SENSOR_2_PIN);
    val3 = digitalRead(SENSOR_3_PIN);
    buttonPinVal = digitalRead(BUTTON_PIN);

// If the frame check interrupt hasn't yet dealt with a tickNow event, make sure you don't erase that tick
// Since nobody will ever drive the sensor faster than 500Hz (250 actual ticks/second),
// the frame check interrupt will never get multiple ticks on a single sensor.
//
// Previously this code did not check, causing ticks to be erased if another pin changed before the frame check
// interrupt serviced the appropriate tickNow flag

    if (!racer1TickNow) racer1TickNow = ((val0 == false) && (lastSensor0Value == true));
    if (!racer2TickNow) racer2TickNow = ((val1 == false) && (lastSensor1Value == true));
    if (!racer3TickNow) racer3TickNow = ((val2 == false) && (lastSensor2Value == true));
    if (!racer4TickNow) racer4TickNow = ((val3 == false) && (lastSensor3Value == true));
    if (!buttonNow) buttonNow = ((buttonPinVal == false) && (lastButtonValue == true));

    lastSensor0Value = val0;  // now that you've used this value of val#, make sure it's recorded as the standing value...
    lastSensor1Value = val1;
    lastSensor2Value = val2;
    lastSensor3Value = val3;
    lastButtonValue = buttonPinVal;
    
    inputChange = true;
    
    // Reenable interrupts
    sei();
}

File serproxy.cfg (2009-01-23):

# Config file for serproxy
# See serproxy's README file for documentation

# Transform newlines coming from the serial port into nils
# true (e.g. if using Flash) or false
newlines_to_nils=true

# Comm ports used
comm_ports=1
serial_device1=/dev/ttyUSB0

# Default settings
comm_baud=115200
comm_databits=8
comm_stopbits=1
comm_parity=none

# Idle time out in seconds
timeout=300

# Port 1 settings (ttyS0)
net_port1=5331

# Port 2 settings (ttyS1)
net_port2=5332

# Port 3 settings (ttyS2)
net_port3=5333

# Port 4 settings (ttyS3)
net_port4=5334

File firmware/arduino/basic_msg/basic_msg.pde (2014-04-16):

/*
 * Arduino wiring:
 *
 * Digital pin  Connected to
 * -----------  ------------
 * 2            Sensor 0
 * 3            Sensor 1
 * 4            Sensor 2
 * 5            Sensor 3
 *
 * 9            Racer0 Start LED anode, Stop LED cathode
 * 10           Racer1 Start LED anode, Stop LED cathode
 * 11           Racer2 Start LED anode, Stop LED cathode
 * 12           Racer3 Start LED anode, Stop LED cathode
 *
 */

int statusLEDPin = 13;
long statusBlinkInterval = 250;
int lastStatusLEDValue = LOW;
long previousStatusBlinkMillis = 0;

boolean raceStarted = false;
boolean raceStarting = false;
boolean mockMode = false;
unsigned long raceStartMillis;
unsigned long currentTimeMillis;

int val = 0;

int racer0GoLedPin = 9;
int racer1GoLedPin = 10;
int racer2GoLedPin = 11;
int racer3GoLedPin = 12;

int sensorPins[4] = {2,3,4,5};
int previoussensorValues[4] = {HIGH,HIGH,HIGH,HIGH};
int values[4] = {0,0,0,0};
unsigned long racerTicks[4] = {0,0,0,0};
unsigned long racerFinishTimeMillis[4];

unsigned long lastCountDownMillis;
int lastCountDown;

unsigned int charBuff[8];
unsigned int charBuffLen = 0;
boolean isReceivingRaceLength = false;

int raceLengthTicks = 20;
int previousFakeTickMillis = 0;

int updateInterval = 250;
unsigned long lastUpdateMillis = 0;

void setup() {
  Serial.begin(115200);
  pinMode(statusLEDPin, OUTPUT);
  pinMode(racer0GoLedPin, OUTPUT);
  pinMode(racer1GoLedPin, OUTPUT);
  pinMode(racer2GoLedPin, OUTPUT);
  pinMode(racer3GoLedPin, OUTPUT);
  digitalWrite(racer0GoLedPin, LOW);
  digitalWrite(racer1GoLedPin, LOW);
  digitalWrite(racer2GoLedPin, LOW);
  digitalWrite(racer3GoLedPin, LOW);
  for(int i=0; i<=3; i++)
  {
    pinMode(sensorPins[i], INPUT);
    digitalWrite(sensorPins[i], HIGH);
  }

}

void blinkLED() {
  if (millis() - previousStatusBlinkMillis > statusBlinkInterval) {
    previousStatusBlinkMillis = millis();

    lastStatusLEDValue = !lastStatusLEDValue;

    digitalWrite(statusLEDPin, lastStatusLEDValue);
  }

}

void raceStart() {
  raceStartMillis = millis();
}


void checkSerial(){
  if(Serial.available()) {
    val = Serial.read();
    if(isReceivingRaceLength) {
      if(val != '\r') {
        charBuff[charBuffLen] = val;
        charBuffLen++;
      }
      else if(charBuffLen==2) {
        // received all the parts of the distance. time to process the value we received.
        // The maximum for 2 chars would be 65 535 ticks.
        // For a 0.25m circumference roller, that would be 16384 meters = 10.1805456 miles.
        raceLengthTicks = charBuff[1] * 256 + charBuff[0];
        isReceivingRaceLength = false;
        Serial.print("OK ");
        Serial.println(raceLengthTicks,DEC);
      }
      else {
        Serial.println("ERROR receiving tick lengths");
      }
    }
    else {
      if(val == 'l') {
          charBuffLen = 0;
          isReceivingRaceLength = true;
      }
      if(val == 'v') {
        Serial.println("basic-1");
      }
      if(val == 'g') {
        for(int i=0; i<=3; i++)
        {
          racerTicks[i] = 0;
          racerFinishTimeMillis[i] = 256*0;
        }

        raceStarting = true;
        raceStarted = false;
        lastCountDown = 4;
        lastCountDownMillis = millis();
      }

      else if(val == 'm') {
        // toggle mock mode
        mockMode = !mockMode;
      }

      if(val == 's') {
        raceStarted = false;

        digitalWrite(racer0GoLedPin,LOW);
        digitalWrite(racer1GoLedPin,LOW);
        digitalWrite(racer2GoLedPin,LOW);
        digitalWrite(racer3GoLedPin,LOW);
      }
    }
  }
}

void printStatusUpdate() {
  if(currentTimeMillis - lastUpdateMillis > updateInterval) {
    lastUpdateMillis = currentTimeMillis;
    for(int i=0; i<=3; i++)
    {
      Serial.print(i);
      Serial.print(": ");
      Serial.println(racerTicks[i], DEC);
    }
    Serial.print("t: ");
    Serial.println(currentTimeMillis, DEC);
  }
}

void loop() {
  blinkLED();

  checkSerial();


  if (raceStarting) {
    if((millis() - lastCountDownMillis) > 1000){
      lastCountDown -= 1;
      lastCountDownMillis = millis();
    }
    if(lastCountDown == 0) {
      raceStart();
      raceStarting = false;
      raceStarted = true;

      digitalWrite(racer0GoLedPin,HIGH);
      digitalWrite(racer1GoLedPin,HIGH);
      digitalWrite(racer2GoLedPin,HIGH);
      digitalWrite(racer3GoLedPin,HIGH);
    }
  }
  if (raceStarted) {
    currentTimeMillis = millis() - raceStartMillis;

    for(int i=0; i<=3; i++)
    {
      if(!mockMode) {
        values[i] = digitalRead(sensorPins[i]);
        if(values[i] == HIGH && previoussensorValues[i] == LOW){
          racerTicks[i]++;
          if(racerFinishTimeMillis[i] == 0 && racerTicks[i] >= raceLengthTicks) {
            racerFinishTimeMillis[i] = currentTimeMillis;
            Serial.print(i);
            Serial.print("f: ");
            Serial.println(racerFinishTimeMillis[i], DEC);
            digitalWrite(racer0GoLedPin+i,LOW);
          }
        }
        previoussensorValues[i] = values[i];
      }
      else {
        if(currentTimeMillis - lastUpdateMillis > updateInterval) {
          racerTicks[i]+=(i+1);
          if(racerFinishTimeMillis[i] == 0 && racerTicks[i] >= raceLengthTicks) {
            racerFinishTimeMillis[i] = currentTimeMillis;
            Serial.print(i);
            Serial.print("f: ");
            Serial.println(racerFinishTimeMillis[i], DEC);
            digitalWrite(racer0GoLedPin+i,LOW);
          }
        }
      }
    }
  }


  if(racerFinishTimeMillis[0] != 0 && racerFinishTimeMillis[1] != 0 && racerFinishTimeMillis[2] != 0 && racerFinishTimeMillis[3] != 0){
    if(raceStarted) {
      raceStarted = false;
      printStatusUpdate();
    }
  } else {
    printStatusUpdate();
  }
}

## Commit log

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2007-03-06 changed sensor.rb to write to logfile. Fixed distance calculation/display.
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2007-03-31 Refactored the distances a bit to make math easier and more apparent. THIS IS THE LAST PEER-REVIEWED CHECKIN BEFORE RELEASE. revert in case of emergency.
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2007-09-27 FW update: improved the time stamp format to prevent overflow at around 6 mins. the new format for a sensor event message (tick) is as follows:
    riderNumber;minutesElapsed:hundredthsSecondsElapsed
    the line ends with a carriage return. FW is now at ver 0.31
    next item to do: test mode which randomly or periodically sends fake ticks to the PC app.
2007-09-29 FW update: * added test mode feature. A fake sensor event message is sent to the PC every 10 centiseconds. the sensor event messages alternate between bike 1 (sensor 0) and bike 2 (sensor 1). the tes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
    * cleaned up the code some
    * fixed a bad yet hidden bug that could make bike 2 (sensor 0) have a disadvantage.
    * FW version bumped to 0.32
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2008-01-29 Merged the mock_hall_effect_sensor into trunk from the cairo branch. It only works for one race for some reason.
    Wheel diameter is now 'roller_diameter'.
    Error message when shoes is not found.
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2008-04-29 fixed HW directory again
    [roller_sensor.brd, roller_sensor.sch]
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2008-05-08 roller sensor board v02: generated schematic. To Do - make **pin** device
    [roller_sensor.brd, roller_sensor.sch]
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2008-06-25 HW: sensor_board v02: almost done with the layout. see NOTES.txt for remaining to do items.
    [roller_sensor.brd, roller_sensor.sch]
2008-06-25 HW: roller_sensors_v02: added thruholes. need to route them. need to decrease the size of their symbol
    [roller_sensor.brd, roller_sensor.sch]
2008-06-29 HW roller sensors, almost there. Eagle still throwing some errors.
    [roller_sensor.brd, roller_sensor.sch]
2008-07-02 HW: roller sensor board: redoing the board so that it's synchronized to the schematic.
    [roller_sensor.brd, roller_sensor.sch]
2008-07-02 HW: roller sensor board: Schematic Complete. Need to lay traces on board. removed extraneous parts from roller_sensor.lbr
    [roller_sensor.brd, roller_sensor.sch]
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2008-07-06 Fixed the "Quit Race" button and moved interface module into it's own file.
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2008-07-07 HW: roller sensor v02: * corrected pin connections on Hall Effect Sensor package. * layout may be finished. NEXT: * screw holes - (4) x 440 for possible daughter board to mate with signals from ether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
    [roller_sensor.brd, roller_sensor.sch]
2008-07-07 HW: roller sensors v02: added drill holes NEXT: * verify diameters and placement of screw holes
    [roller_sensor.brd]
2008-07-08 HW: roller sensors v02: layout is finished. ready to create Gerber files.
    [roller_sensor.brd]
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2008-07-08 HW: roller sensors v02: not sure why, but gerber output format is wrong.
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2008-07-08 restart the board. i was unhappy with the parts being off the grid.
    [roller_sensor.brd]
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2008-07-08 New version of board completed. This time it uses library packages from SparkFun (8-pin header and 4-40 screw holes)
    [roller_sensor.sch]
2008-07-08 New version of board completed. This time it uses library packages from SparkFun (8-pin header and 4-40 screw holes) ---- board file added to index.
    [roller_sensor.brd]
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2008-07-09 Fixed conf-sample.yml to more closely model the stucture that I actually expect.
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2008-07-10 HW: roller sensor: PCB: * moved RJ45 jack and surrounding components north, closer to the HE sensor. Left enough room to run a zip tie between them. * changed strain relief holes to 4-40 size, and ch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
    [roller_sensor.brd, roller_sensor.sch]
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2008-07-15 moved HW -> hardware, got rid of v01 and v02. Now just one main directory for development of the sensor board.
    [roller_sensor.brd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]
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2008-07-15 hopefully fixed the HE sensor wiring in the eagle library
2008-07-16 roller sensor PCB v03: added 1 more RJ45 jack. removed diode and On LED indicator. * traces laid by autorouter seem messed up. need to fix some trace routing problems.
    [roller_sensor.brd, roller_sensor.sch]
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2008-07-18 Added a mock routine to the arduino and the corresponding computer driver. Fixed weird LED progress bug with the sheer force of dumb repetitive conditionals.
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2008-07-21 roller sensor board: * fixed an error in Hall effect sensor package * changed date on silkscreen * created Eagle design rule check (DRC) file advanced_circuits_Luke.dru
    [roller_sensor.brd, roller_sensor.sch]
2008-07-21 roller sensor board: * lengthened board and made larger drill holes. * now about to clean out gerber files from the repository.
    [roller_sensor.brd, roller_sensor.sch]
2008-07-21 roller sensor board: * cleaned up old gerber files * cleaned up backup files
    [roller_sensor.brd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]
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2008-07-21 roller sensors: * updated .cam file to save gerber files in gerber/ directory.
    [roller_sensor.GBL, roller_sensor.GBO, roller_sensor.GBS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]
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2008-07-22 roller sensor board:
    * generated new gerber files from the eagle-provided cam file gerb274x.cam
    [roller_sensor.GBL, roller_sensor.GBO, roller_sensor.GBS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]
2008-07-22 roller sensor board: move the long traces over to fit a large drill hole (at least 0.25") for a zip tie.
    [roller_sensor.brd, roller_sensor.sch]
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2008-07-23 arduino firmware: * start indexing rider/sensor/val names with 0 instead of 1 e.g. rider1 is now rider0, and sensor2 is now sensor1. * tick messages sent over serial interface begin with "0:" and "1: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
    NEED to update the PC app to look for "0:" and "1:" instead of "1:" and "2:".
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2008-08-03 - set finish times in race presenter before we draw them - fix tournament recording - make mock arduino act more like real sensor data - main can be run directoy if you have shoes in your path
2008-08-05 roller sensor hardware: * changed the pinout of the RJ45 as follows: 1 - VCC 2 - GND 3 - VOUT 4 - AUX0 5 - AUX1 6 - AUX2 7 - AUX3 8 - AUX4
    [roller_sensor.brd, roller_sensor.sch]
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2008-08-27 started creating roller sensor board in kicad created custom module for s441a hall effect sensor kicad
    [$savepcb.brd, roller_sensor.brd, roller_sensor.sch]
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2008-09-01 corrected the schematic, created netlist for interface board
    [interface_board.sch]
2008-09-01 interface board nearly finished. need to figure out how to make board dimensions. :
    [$savepcb.brd, interface_board.brd, noname.brd]
2008-09-01 interface board: added VCC and GND conns to schematic. Now go update the board.
    [interface_board.sch]
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2008-09-03 new interface board layout completed. need to verify that the arduino and UBW will both fit on the board.
    [$savepcb.brd, interface_board.brd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]
2008-09-03 with this version, released the interface board design to barebonespcb.com. the files submitted are in interface_board_gerb_200809021359.zip
    [$savepcb.brd, interface_board.brd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]
2008-09-08 roller sensor: new updated version in completed (almost) in Kicad. - added another 8 pin header so that the PCB can be cut in half if necessary. - need to add 8 (?) screw holes
    [$savepcb.brd, roller_sensor.brd, roller_sensor.sch]
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2008-10-15 Removed some sensors that I no longer plan to support. All arduino, baby.
2008-10-17 Fixed some stuff I broke while ripping out the tournament data and/or getting things working with morgan's new sensor.
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2008-11-02 hardware: interface board: resized PCB size to fit in Serpac A-31 housing. need to move holes and rest of components.
    [$savepcb.brd, interface_board.brd]
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2008-11-06 hardware: interface board: finished the schematic for now. need to create layout modules HEADER_100MIL_6x1 and HEADER_100MIL_8x1 and ARDUINO_USB_MODULE
    [interface_board.sch]
2008-11-06 hardware: interface board: created modules in project directory. created layout modules HEADER_100MIL_6x1 and HEADER_100MIL_8x1. need to create layout module for the arduino module/shield
    [$savepcb.brd, interface_board.brd]
2008-11-08 hardware: interface board: now have footprints made for the arduino USB module and 8 pin connectors. need to fix some of their bugs.
    [interface_board.brd]
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2008-11-09 hardware: interface board: replaced old footprints with new ones.
    [$savepcb.brd, interface_board.brd, interface_board.sch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]
2008-11-10 interface board: kicad was mysteriously creating ratsnest wires between pins 1 and 2 on some of the 8 pin connectors. because i couldn't figure out how to fix that, i have started learning gEDA.
    [$savepcb.brd, interface_board.brd, interface_board.sch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]
2008-11-10 interface board: first draft of the schem, completed using gEDA instead of kicad
    [interface_board.sch]
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2008-11-14 morgan's opensprints sensor debugged firmware: Symptom: some ticks get missed -- timing of the frames is always correct, but input "abababababab" sometimes comes out as "ababaaababab" -- one of the b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
    The behavior is correlated to floating the other sensor pins. When
    they float, they generate occasional random GPIO interrupts.
    This, in turn, causes the code in the interrupt handler to be executed.
    The overarching interrupt structure is as follows (Evan, this may help
    clarify the convoluted code ;) ):
    2ms Frame interrupt:
    Happens every 2ms.
    This is fast enough that no sensor will ever tick twice during a
    Frame (500Hz = >250mph)
    Actions:
    Check each sensor to see i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
2008-11-15 interface board: creating the package ARDUINO_USB_EXPANSION.fp kind of worked and it is in the interface board layout now.
    [interface_board.sch]
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2008-11-17 interface board: added headers - pins connected to all of the arduino pins. created new symbol for 6 x 1 header.
    [interface_board.sch]
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2008-11-17 interface board: edited the pcb layout. need to correct the footprint for the arduino connector. there are 2 pin 27s :<(
2008-11-17 interface board: corrected footprint for arduino connectors
2008-11-17 interface board: corrected the ARDUINO USB footprint and replaced it in the pcb layout.
    [interface_board.sch]
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2008-11-18 calibrated printer and printed the board. dimensions are correct. needed to extend the South edge of the board out 0.12" more. The footprint for the Arduino is mirror L to R, so need to correct that.
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2008-11-18 interface board: finally got nets to be correct. watch out for hidden text in symbols
    [interface_board.sch]
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2008-11-19 interface board: geda: cannot update the footprint for the USB module without causing errors. kicad: mysterious rat connecting 5V supply and GND on P1 and P4 won't go away.
    [interface_board.sch]
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2008-11-24 Added a "call it button" to record scores in the event of a technical malfunction or quitter. Also, before there was a bug where e.g. a you couldn't race just two people when four bikes had been conf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
2008-11-26 interface board: grid of pins but solder mask is currently covering them.
    needs text:
    * label signals
    - 5V
    - GND
    - Rider1, ...
    * name of board and designer, etc.
    Need to update NOTES.txt:
    * clearance is 20, not 0.
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2008-12-04 interface board: inner columns of pads inside arduino headers. drew some lines in top copper because probably won't be any silk. TODO: finish labels for signal on each RJ45/assoc. header
2008-12-08 roller sensor board: replaced outdated pdf with current version.
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2008-12-09 roller sensor: practically done unless anyone has any last-minute issues
    [roller_sensor.brd, roller_sensor.sch]
2008-12-10 roller sensor: corrected freedfm issue with '2008' text too close to hole
    [roller_sensor.brd]
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2008-12-11 1. ordered interface and sensor boards using barebones gerber files in this commit. 2. cleaned out PCB development from other tools that didn't get used ultimately 3. see the pdfs in each pcb directo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
    [$savepcb.brd, interface_board.brd, interface_board.sch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]
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2008-12-15 Fixed some hilarious bugginess introduced when the basic_msg firmware was moved to 4 racers.
    [basic_msg.pde]
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2008-12-28 corrected the sensor board. changed version to v2.1. Tick indicator LED now connects to signal VOUT instead of GND. Improving the Makefile is a WIP.
    [roller_sensor.brd, roller_sensor.sch]
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2009-01-24 advanced message bugfix -- reset time command was not clearing the outgoing packet immediately
    this was resulting in pre-start data getting sent after the reset
    command. existing packet is now cleared on "g" command.
    [advanced_msg.cpp, advanced_msg.pde]
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2009-01-31 Resolved the problem with bike color names needing to be lower case
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2009-02-20 BUG: the race wasn't ending since my last change on Mon Jan 26 23:41:01 2009 -0600. Please re-flash your firmware if you have any firmware from between 1/26 and 2/19.
    [basic_msg.pde]
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2009-03-02 more descriptive error message from Shoes when Arduino is not connected and using basic_msg FW.
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2009-03-08 Sorry network sensor users. Fixes the bug where the first bike doesn't worl
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2009-03-16 Replaced the redblue shuffle button with sortable list.
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2009-03-20 firmware: fixed bug - if race is already running sending the 'go' command would not restart the countdown timer.
    new feature: send the character 'm' to activate mock sensor readings.
    charBuff[8] and charBuffLen changed to type unsigned int
    [basic_msg.pde]
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2009-05-26 interface board is finished. clean, no DRC errors. I could change net names back to words instead of numbers.
    [interface_board.brd, interface_board.sch, interface_board_sh1.sch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]
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2009-05-26 interface PCB: DONE: slight adjustments to layout, show dimensions, generated gerber plots, output.zip TODO: resolve missing soldermask over holes.
    [interface_board.brd, interface_board.sch, interface_board_sh2.sch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]
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2009-06-01 evaluated interface board v2.3.0 - RJ45 holes for plastic tabs too far apart. fixed the footprint and pcb layout. bumped to v2.3.1
    [interface_board.brd]
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2009-06-06 roller sensor: ordered barebones PCBs with this version of roller_sensor_barebones_output.zip. changes: added text in copper layers, proto area. I prefer older version of Kicad 20090216 for its block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
    [roller_sensor.brd, roller_sensor.sch]
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2009-08-23 Broke the sample data into its own file.
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2009-09-15 Fixes upgrade button.
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2009-09-19 Adds an edit button to the racers, changes how to edit races, adds a swap button when the number of racers is two.
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2009-09-20 removes the main menu button from stats, fixes 'New Race' button.
2009-09-21 Weird datamapper bug with filter by tournament_id.
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2009-09-21 Changes hide/show finished to a button to fix zombie checkbox. Fixes titles on config.
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2009-09-23 firmware - send 'm' to toggle Arduino mock mode. that message no longer starts a race.
    [basic_msg.pde]
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2009-09-30 Revert "hardware: sensor panel now has numbers"
    This reverts commit c53c1b80e1ce7b33996befee0afbbaad7fa46776.
    [panel-sensors.dxf]
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2009-11-13 removed arduino makefile because it doesn't work
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2010-09-23 fixes bug in mock sensor and bike finish times on clock race screen
2014-04-27 Characterize setting length correctly in firmware test
    [test_pyserial_basic_msg.py]
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
